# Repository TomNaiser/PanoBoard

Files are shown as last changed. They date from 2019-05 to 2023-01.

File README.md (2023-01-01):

# PanoBoard
Integrated Electronics Board for a Gigapixel Panorama Head (pan and tilt motion)
-Arduino nano based controller
-bluetooth communication with the windowsbased control notebook
-PID position control (modified RC-Servos)
-rotatory position encoders for precise position control 

The latest version PanoBoardV5 is a size-reduced version. With the shrunken electronics box the panorama rig fits into my photo backpack. 

Warning! The circuits in this project were designed as a hobbyist project and may contain unintentional mistakes.  I don't take any responsibility for damages caused by using the above circuit design. Please use the provided information at your own risk!

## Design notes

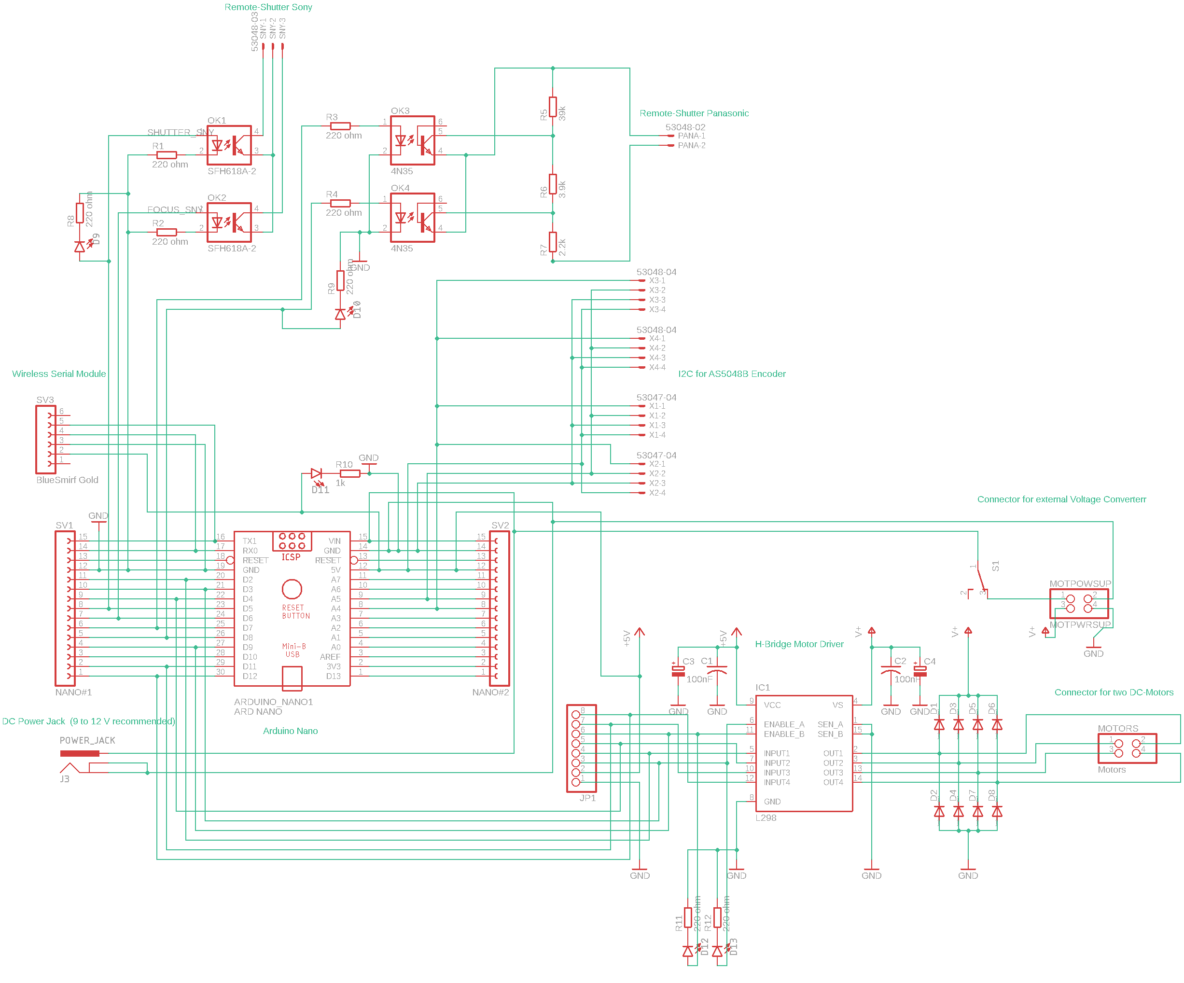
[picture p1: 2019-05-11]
PanoBoardSchematic.png

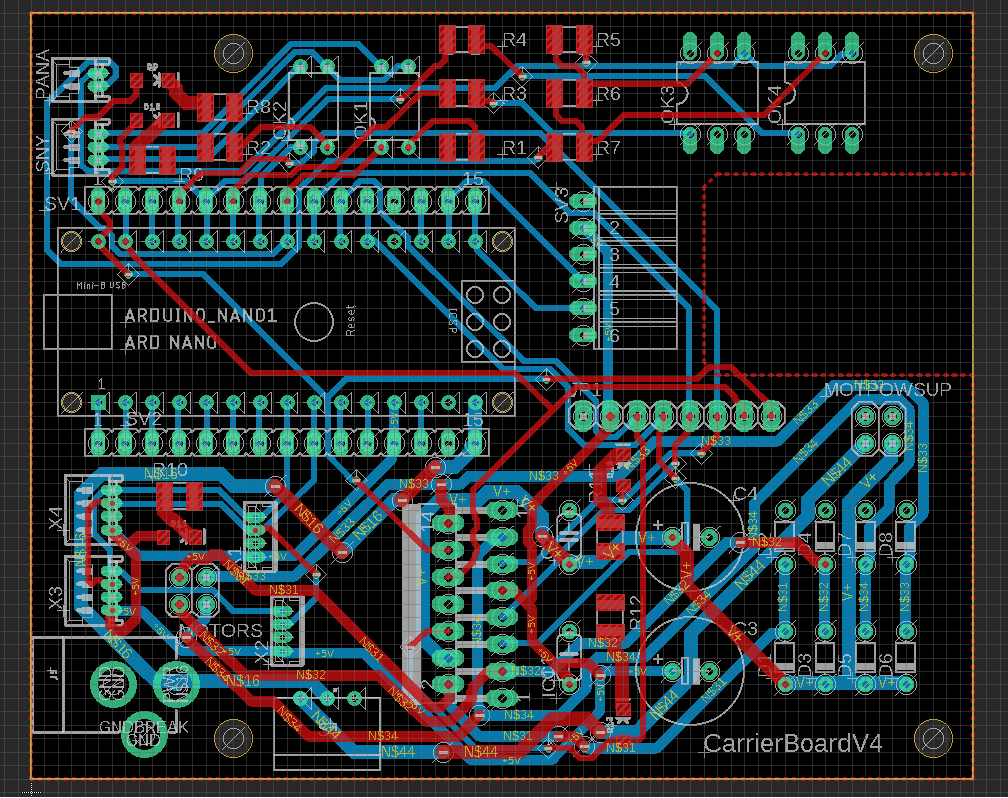
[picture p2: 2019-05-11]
PanoBoardV4_BoardLayout.PNG

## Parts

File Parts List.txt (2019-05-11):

From Amazon:
Arduino Nano Clone (1 piece)

Slide-Switch, MINI, ON-ON, RIGHT ANGLE 450302014072 By WURTH ELEKTRONIK  (1 piece)

SHOOT Rm-vpr1 remote shutter switch for Sony cameras (1 piece) (diassemble, you only need the connector to the camera, which looks like a usb, but actually isn't one)

Hitec Sail Winch Servo HS-785 HB (2 pieces)

From Servo City:
TM-700 Servo Gearbox with (I use a gear ratio of 3:1, however possibly 5:1 or 7:1 will enable better positioning accuracy) 
(2 pieces)

From Mouser:

1	
SparkFun Bluetooth Modem - BlueSMiRF Gold 474-WRL-12582  WRL-12582
1 piece

2	
Headers & Wire Housings Headers & Wire Housings 
437-8018300620001101
801-83-006-20-001101

3	
Magnetic Sensor Development Tools Magnetic Sensor Development Tools Adapter Board with I2C Interface
985-AS5048B-TS_EK_AB
AS5048B-TS_EK_AB
Adapter Board
2 pieces	

4	
DC Power Cords DC Power Cords PicoBlade CBL ASSY 14CKT 600MM NTL
538-15134-1406
15134-1406
PicoBlade CBL ASSY
1 or 2 pieces

5	
Headers & Wire Housings Headers & Wire Housings RIGHT ANGLE HDR 4P
538-53048-0410
53048-0410
RIGHT ANGLE HDR 4P

6	
Headers & Wire Housings Headers & Wire Housings VERTICAL HDR 4P
538-53047-0410
53047-0410
VERTICAL HDR 4P

7	
Headers & Wire Housings Headers & Wire Housings RIGHT ANGLE HDR 3P
538-53048-0310
53048-0310
RIGHT ANGLE HDR 3P

8	
Headers & Wire Housings Headers & Wire Housings RIGHT ANGLE HDR 2P
538-53048-0210
53048-0210
RIGHT ANGLE HDR 2P

9	
Headers & Wire Housings Headers & Wire Housings RECEPTACLE 4 POS
538-51021-0400
51021-0400
RECEPTACLE 4 POS

10	
Headers & Wire Housings Headers & Wire Housings RECEPTACLE 3 POS
538-51021-0300
51021-0300
RECEPTACLE 3 POS

11	
Headers & Wire Housings Headers & Wire Housings RECEPTACLE 2P
538-51021-0200
51021-0200
RECEPTACLE 2P

12	
SparkFun Accessories SparkFun Accessories DC Barrel Power Jack/Connector
474-PRT-00119
PRT-00119
1 piece

13	
Motor/Motion/Ignition Controllers & Drivers Motor/Motion/Ignition Controllers & Drivers Dual Full Bridge
511-L298
L298N
Dual Full Bridge
1 piece

14	
Transistor Output Optocouplers Transistor Output Optocouplers PTR 100%, 3.5KV
859-4N35
4N35
PTR 100%, 3.5KV
2 pieces

15	
Transistor Output Optocouplers Transistor Output Optocouplers Phototransistor Out Single CTR 63-125%
782-SFH618A-2
SFH618A-2
Phototransistor Out
2 pieces

16	
Schottky Diodes & Rectifiers Schottky Diodes & Rectifiers Vr/40V Io/1A AMMO
511-1N5819
1N5819
Vr/40V Io/1A AMMO
8 pieces

17	
Aluminium Electrolytic Capacitors - Radial Leaded Aluminium Electrolytic Capacitors - Radial Leaded 50volts 0.1uF 4x7 20% 1.5LS
647-USP1H0R1MDD
USP1H0R1MDD
50volts 0.1uF
2 pieces

18	
Aluminium Electrolytic Capacitors - Radial Leaded Aluminium Electrolytic Capacitors - Radial Leaded 100UF 100V
661-EKMQ101ELL101MJ1
EKMQ101ELL101MJ16S
100UF 100V
2 pieces

19	
Thick Film Resistors - SMD Thick Film Resistors - SMD 1210 220ohms 1% AEC-Q200667-ERJ-14NF2200U
ERJ-14NF2200U
1210 220ohms

20	
Thick Film Resistors - SMD Thick Film Resistors - SMD 1210 39Kohm 1% High Voltage
755-KTR25JZPF3902
KTR25JZPF3902
1210 39Kohm 1%

21	
Thick Film Resistors - SMD Thick Film Resistors - SMD 1210 3.9Kohms 1% AEC-Q200
667-ERJ-14NF3901U
ERJ-14NF3901U
1210 3.9Kohms

22	
Thick Film Resistors - SMD Thick Film Resistors - SMD 1210 2.2Kohms 5% AEC-Q200
667-ERJ-14YJ222U
ERJ-14YJ222U
1210 2.2Kohms

23	
Thick Film Resistors - SMD Thick Film Resistors - SMD CRGP 1210 1K0 1% SMD Resistor
279-CRGP1210F1K0
CRGP1210F1K0
CRGP 1210 1K0 1%

24	
Thick Film Resistors - SMD Thick Film Resistors - SMD CRGCQ 1210 2K7 1% SMD Resistor
279-CRGCQ1210F2K7
CRGCQ1210F2K7
CRGCQ 1210 2K7 1%

25	
Standard LEDs - SMD Standard LEDs - SMD 3.2X1.6MM LOW CRNT
604-APT3216LZGCK
APT3216LZGCK
3.2X1.6MM LOW CRNT

26	
Headers & Wire Housings Headers & Wire Housings 
437-8018705010001101
801-87-050-10-001101

27	
Headers & Wire Housings Headers & Wire Housings 25+25 DIL VERTICAL PIN HEADER GOLD HT
855-M20-9722545
M20-9722545
25+25 DIL VERTICAL

28	
Headers & Wire Housings Headers & Wire Housings 2.54MM 0.1" 15-PIN FEMALE HEADER
992-15FX1-254MM
15Fx1-254mm
2.54MM 0.1" 15-PIN

29	
Headers & Wire Housings Headers & Wire Housings KK 100 Hdr Assy RA B y RA Bkwy 06 Ckt Tin
538-22-28-7061
22-28-7061
KK 100 Hdr Assy RA B

30	
Headers & Wire Housings Headers & Wire Housings 50P SINGLE ROW
571-5-826629-0
5-826629-0
50P SINGLE ROW

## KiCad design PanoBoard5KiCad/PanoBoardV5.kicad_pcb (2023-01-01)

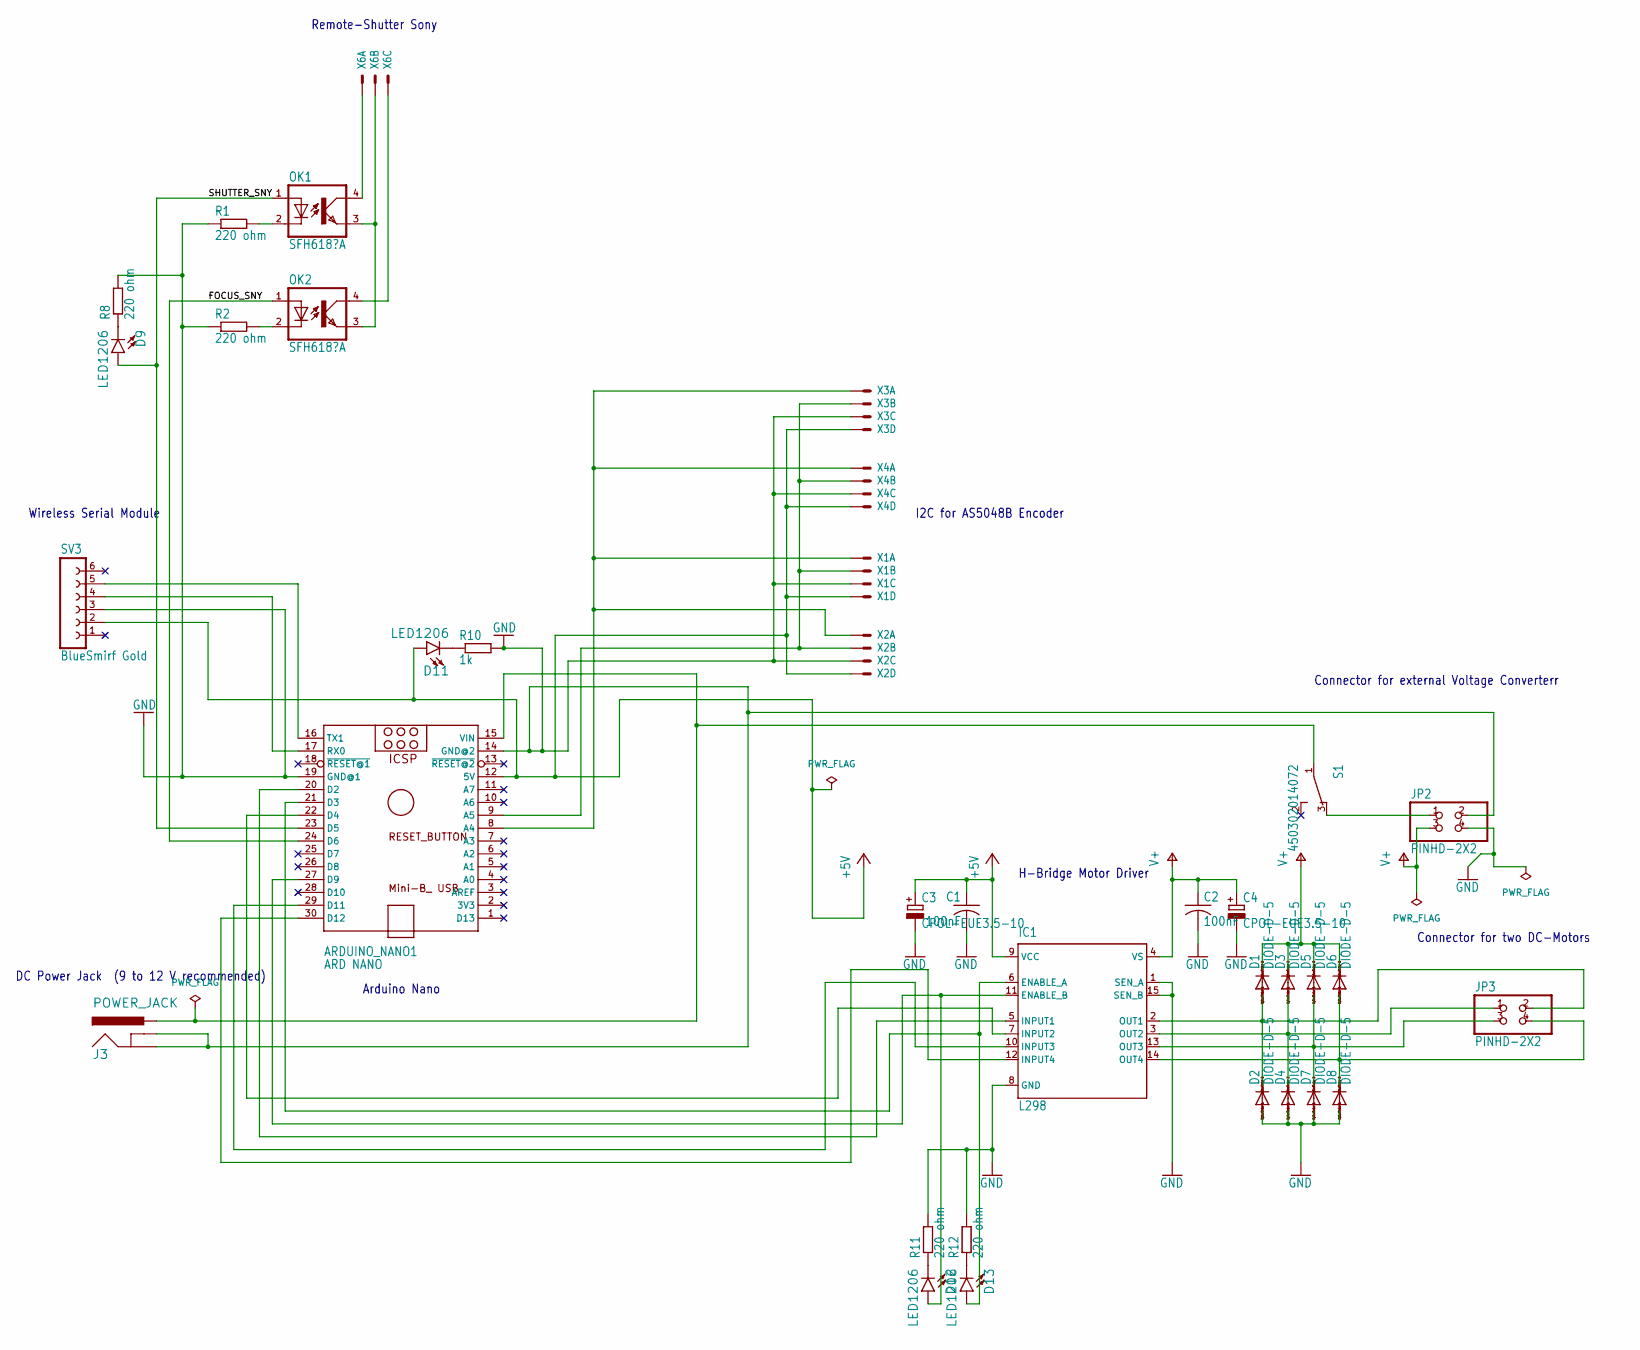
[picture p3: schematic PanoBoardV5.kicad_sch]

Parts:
ARDUINO_NANO1: ARD NANO; ARDUINO_NANO
C1, C2: 100nF; C050-024X044
C3, C4: CPOL-EUE3.5-10; E3,5-10
D1, D2, D3, D4, D5, D6, D7, D8: DIODE-D-5; D-5
D9, D11, D12, D13: LED1206; LED-1206
IC1: L298; MULTIWATT-15
J3: POWER_JACK; POWER_JACK_PTH
JP2, JP3: PINHD-2X2; 2X02
OK1, OK2: SFH618?A; DIP4
R1, R2, R8, R11, R12: 220 ohm; R1210
R10: 1k; R1210
S1: 450302014072
SV3: BlueSmirf Gold; FE06W
X1, X2: 53?-04047; 53047-04
X3, X4: 53?-04048; 53048-04
X6: 53?-03048; 53048-03

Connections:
+5V: ARDUINO_NANO1.12 (5V), C1.1, C3.+, D11.A, IC1.9 (VCC), SV3.2, X1.4 (S), X2.4 (S), X3.4 (S), X4.4 (S)
/FOCUS_SNY: ARDUINO_NANO1.24 (D6), OK2.1 (A)
/SHUTTER_SNY: ARDUINO_NANO1.23 (D5), D9.A, OK1.1 (A)
GND: ARDUINO_NANO1.14 (GND@2), ARDUINO_NANO1.19 (GND@1), C1.2, C2.2, C3.-, C4.-, D2.A, D4.A, D7.A, D8.A, IC1.1 (SEN_A), IC1.8 (GND), IC1.15 (SEN_B), J3.GND, J3.GNDBREAK, JP2.2, JP2.4, R1.1, R2.1, R8.2, R10.2, R11.2, R12.2, SV3.3, X1.3 (S), X2.3 (S), X3.3 (S), X4.3 (S)
unnamed: ARDUINO_NANO1.8 (A4), X1.1 (S), X2.1 (S), X3.1 (S), X4.1 (S)
unnamed: ARDUINO_NANO1.9 (A5), X1.2 (S), X2.2 (S), X3.2 (S), X4.2 (S)
unnamed: ARDUINO_NANO1.15 (VIN), J3.PWR, S1.1
unnamed: ARDUINO_NANO1.16 (TX1), SV3.5
unnamed: ARDUINO_NANO1.17 (RX0), SV3.4
unnamed: ARDUINO_NANO1.20 (D2), IC1.5 (INPUT1)
unnamed: ARDUINO_NANO1.21 (D3), D13.A, IC1.6 (ENABLE_A)
unnamed: ARDUINO_NANO1.22 (D4), IC1.7 (INPUT2)
unnamed: ARDUINO_NANO1.27 (D9), D12.A, IC1.11 (ENABLE_B)
unnamed: ARDUINO_NANO1.29 (D11), IC1.10 (INPUT3)
unnamed: ARDUINO_NANO1.30 (D12), IC1.12 (INPUT4)
unnamed: D1.A, D2.C, IC1.2 (OUT1), JP3.2
unnamed: D3.A, D4.C, IC1.3 (OUT2), JP3.1
unnamed: D5.A, D7.C, IC1.13 (OUT3), JP3.3
unnamed: D6.A, D8.C, IC1.14 (OUT4), JP3.4
unnamed: D9.C, R8.1
unnamed: D11.C, R10.1
unnamed: D12.C, R11.1
unnamed: D13.C, R12.1
unnamed: JP2.1, S1.3
unnamed: OK1.2 (C), R1.2
unnamed: OK1.3 (EMIT), OK2.3 (EMIT), X6.2 (S)
unnamed: OK1.4 (COL), X6.1 (S)
unnamed: OK2.2 (C), R2.2
unnamed: OK2.4 (COL), X6.3 (S)
V+: C2.1, C4.+, D1.C, D3.C, D5.C, D6.C, IC1.4 (VS), JP2.3

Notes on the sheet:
Connector for external Voltage Converterr
I2C for AS5048B Encoder
Connector for two DC-Motors
DC Power Jack (9 to 12 V recommended)
H-Bridge Motor Driver
Remote-Shutter Sony
Wireless Serial Module
Arduino Nano

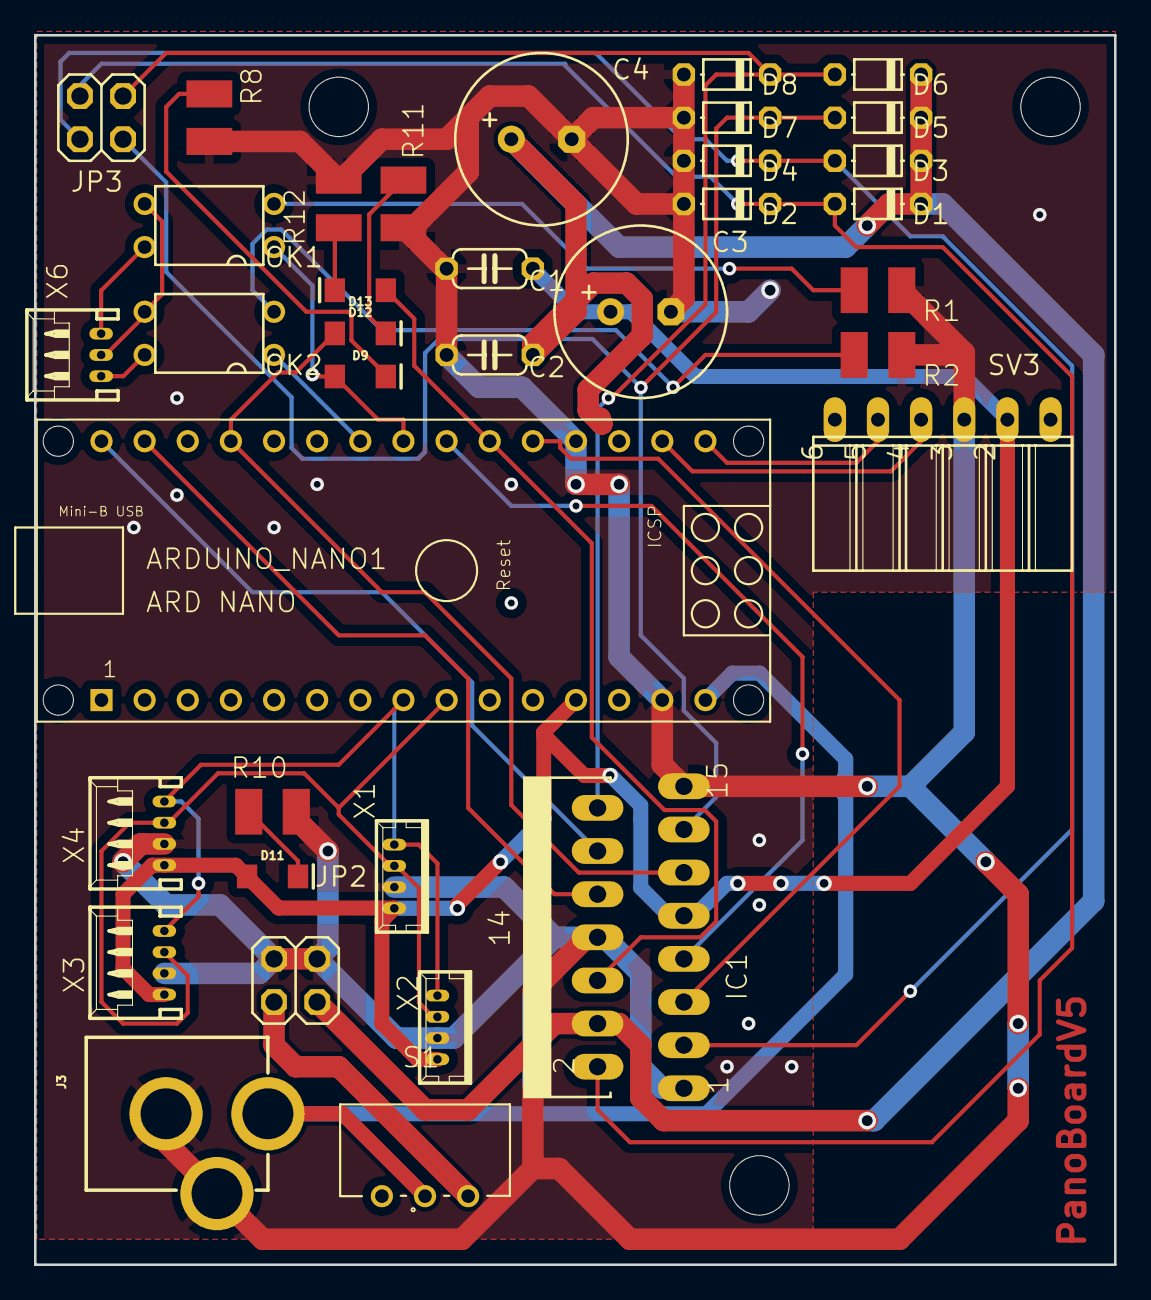
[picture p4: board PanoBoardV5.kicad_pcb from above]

Board: 2 copper layers, 63.6 x 72.4 mm, 39 parts (0 on the bottom side), 30 nets.

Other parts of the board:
@HOLE0, @HOLE2, @HOLE3: (no value)

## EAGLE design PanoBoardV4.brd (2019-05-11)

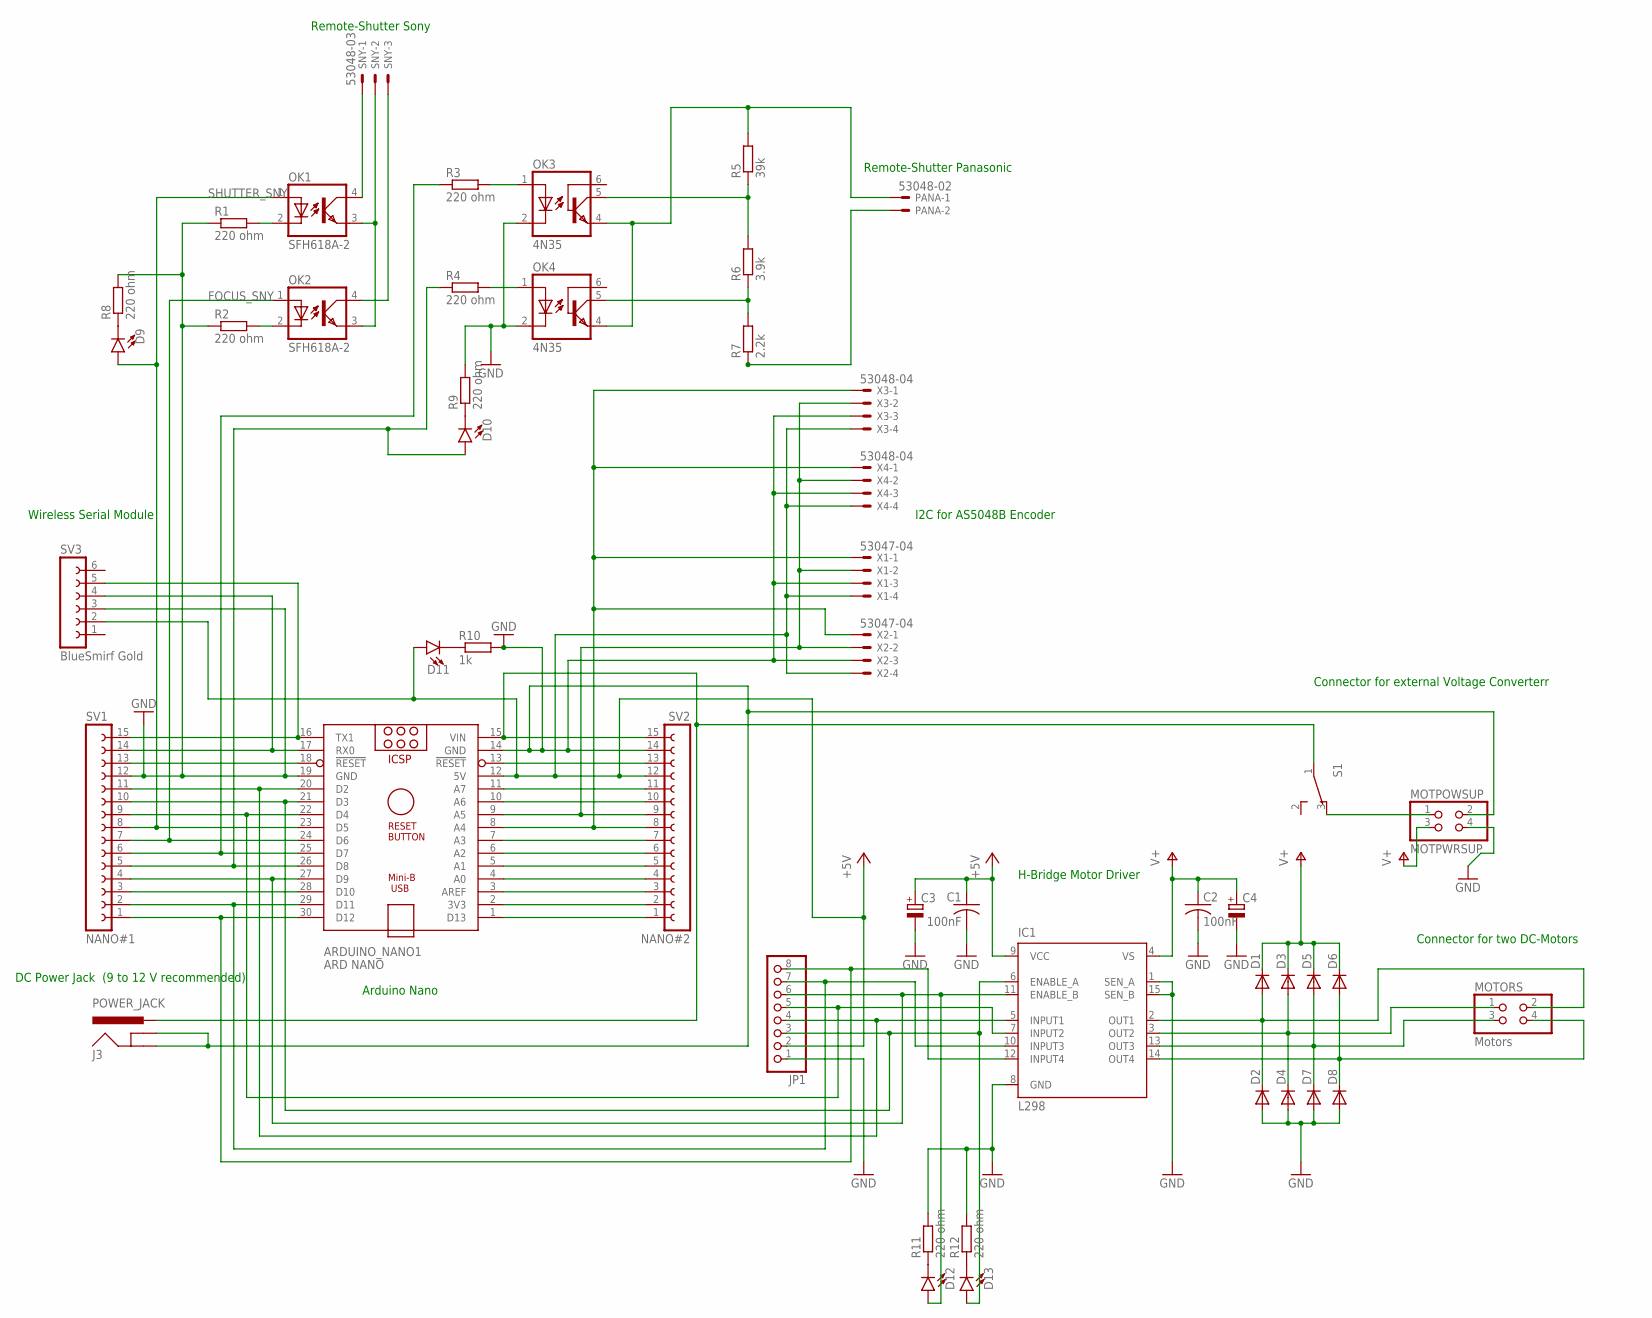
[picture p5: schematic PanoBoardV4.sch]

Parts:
ARDUINO_NANO1: ARD NANO; ARDUINO_NANO
C1, C2: 100nF; C050-024X044
C3, C4: CPOL-EUE3.5-10; E3,5-10
D1, D2, D3, D4, D5, D6, D7, D8: DIODE-D-5; D-5
D9, D10, D11, D12, D13: LED1206; LED-1206
IC1: L298; MULTIWATT-15
J3: POWER_JACK; POWER_JACK_PTH
JP1: PINHD-1X8; 1X08
MOTORS: Motors; 2X02
MOTPOWSUP: MOTPWRSUP; 2X02
OK1, OK2: SFH618A-2; DIP4
OK3, OK4: 4N35; DIL06
PANA: 53048-02
R1, R2, R3, R4, R8, R9, R11, R12: 220 ohm; R1210
R5: 39k; R1210
R6: 3.9k; R1210
R7: 2.2k; R1210
R10: 1k; R1210
S1: 450302014072
SNY: 53048-03
SV1: NANO#1; FE15
SV2: NANO#2; FE15
SV3: BlueSmirf Gold; FE06W
X1, X2: 53047-04
X3, X4: 53048-04

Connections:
+5V: ARDUINO_NANO1.12 (5V), C1.1, C3.+, D11.A, IC1.9 (VCC), JP1.2, SV2.12, SV3.2, X1.4, X2.4, X3.4, X4.4
FOCUS_SNY: ARDUINO_NANO1.24 (D6), OK2.1 (A), SV1.7
GND: ARDUINO_NANO1.14 (GND), ARDUINO_NANO1.19 (GND), C1.2, C2.2, C3.-, C4.-, D2.A, D4.A, D7.A, D8.A, IC1.1 (SEN_A), IC1.8 (GND), IC1.15 (SEN_B), J3.GND, J3.GNDBREAK, JP1.1, MOTPOWSUP.2, MOTPOWSUP.4, OK3.2 (C), OK4.2 (C), R1.1, R2.1, R8.2, R9.2, R10.2, R11.2, R12.2, SV1.12, SV2.14, SV3.3, X1.3, X2.3, X3.3, X4.3
unnamed: ARDUINO_NANO1.16 (TX1), SV1.15, SV3.5
unnamed: ARDUINO_NANO1.17 (RX0), SV1.14, SV3.4
unnamed: ARDUINO_NANO1.18 (!RESET), SV1.13
unnamed: OK1.2 (C), R1.2
unnamed: ARDUINO_NANO1.20 (D2), IC1.5 (INPUT1), JP1.4, SV1.11
unnamed: ARDUINO_NANO1.21 (D3), D13.A, IC1.6 (ENABLE_A), JP1.3, SV1.10
unnamed: ARDUINO_NANO1.22 (D4), IC1.7 (INPUT2), JP1.5, SV1.9
unnamed: OK1.3 (EMIT), OK2.3 (EMIT), SNY.2
unnamed: OK1.4 (COL), SNY.1
unnamed: ARDUINO_NANO1.25 (D7), R3.1, SV1.6
unnamed: ARDUINO_NANO1.26 (D8), D10.A, R4.1, SV1.5
unnamed: ARDUINO_NANO1.27 (D9), D12.A, IC1.11 (ENABLE_B), JP1.6, SV1.4
unnamed: ARDUINO_NANO1.28 (D10), SV1.3
unnamed: ARDUINO_NANO1.29 (D11), IC1.10 (INPUT3), JP1.7, SV1.2
unnamed: ARDUINO_NANO1.30 (D12), IC1.12 (INPUT4), JP1.8, SV1.1
unnamed: ARDUINO_NANO1.15 (VIN), J3.PWR, S1.1, SV2.15
unnamed: OK2.2 (C), R2.2
unnamed: ARDUINO_NANO1.13 (!RESET), SV2.13
unnamed: OK3.1 (A), R3.2
unnamed: ARDUINO_NANO1.11 (A7), SV2.11
unnamed: ARDUINO_NANO1.10 (A6), SV2.10
unnamed: ARDUINO_NANO1.9 (A5), SV2.9, X1.2, X2.2, X3.2, X4.2
unnamed: ARDUINO_NANO1.8 (A4), SV2.8, X1.1, X2.1, X3.1, X4.1
unnamed: ARDUINO_NANO1.7 (A3), SV2.7
unnamed: ARDUINO_NANO1.6 (A2), SV2.6
unnamed: ARDUINO_NANO1.5 (A1), SV2.5
unnamed: ARDUINO_NANO1.4 (A0), SV2.4
unnamed: ARDUINO_NANO1.3 (AREF), SV2.3
unnamed: ARDUINO_NANO1.2 (3V3), SV2.2
unnamed: ARDUINO_NANO1.1 (D13), SV2.1
unnamed: D1.A, D2.C, IC1.2 (OUT1), MOTORS.2
unnamed: D3.A, D4.C, IC1.3 (OUT2), MOTORS.1
unnamed: D6.A, D8.C, IC1.14 (OUT4), MOTORS.4
unnamed: D5.A, D7.C, IC1.13 (OUT3), MOTORS.3
unnamed: OK4.1 (A), R4.2
unnamed: OK2.4 (COL), SNY.3
unnamed: OK3.5 (COL), R5.1, R6.2
unnamed: OK3.4 (EMI), OK4.4 (EMI), PANA.1, R5.2
unnamed: OK4.5 (COL), R6.1, R7.2
unnamed: D9.C, R8.1
unnamed: PANA.2, R7.1
unnamed: D10.C, R9.1
unnamed: D11.C, R10.1
unnamed: MOTPOWSUP.1, S1.3
unnamed: D12.C, R11.1
unnamed: D13.C, R12.1
SHUTTER_SNY: ARDUINO_NANO1.23 (D5), D9.A, OK1.1 (A), SV1.8
V+: C2.1, C4.+, D1.C, D3.C, D5.C, D6.C, IC1.4 (VS), MOTPOWSUP.3

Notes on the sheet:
Remote-Shutter Panasonic
Remote-Shutter Sony
I2C for AS5048B Encoder
H-Bridge Motor Driver
Connector for external Voltage Converterr
Connector for two DC-Motors
Wireless Serial Module
Arduino Nano
DC Power Jack (9 to 12 V recommended)

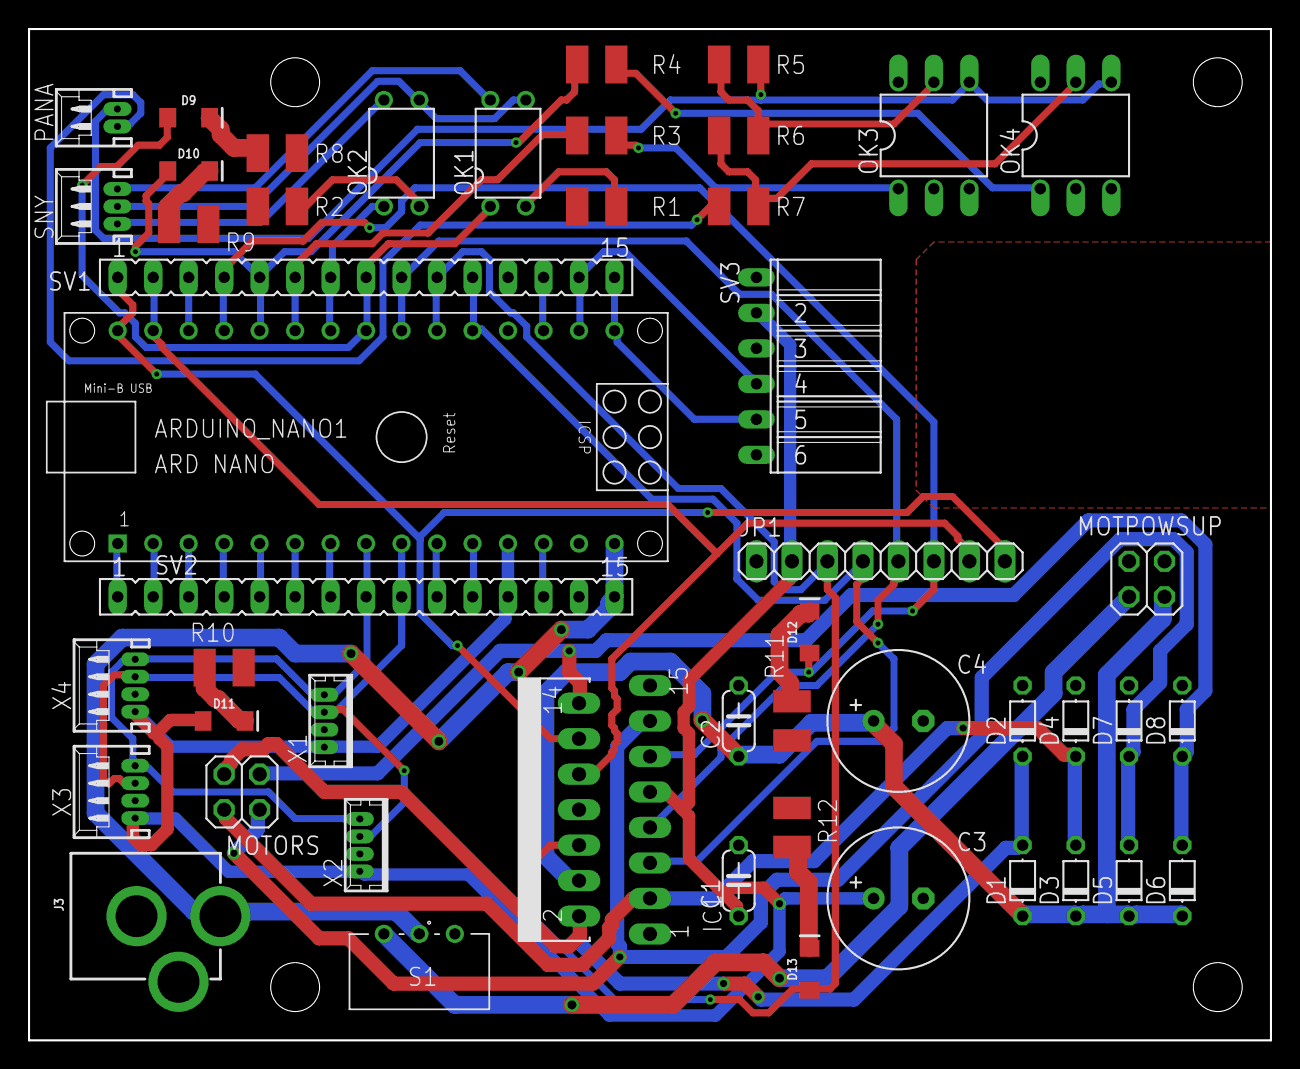
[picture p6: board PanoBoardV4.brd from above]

Board: 2 copper layers, 88.9 x 72.4 mm, 49 parts (0 on the bottom side), 51 nets.

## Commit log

2023-01-01 PanoBoardV5
    Simplified version of the board. Reduced footprint. Camera Triggering support only the Sony A7
    [PanoBoardV5.dsn, PanoBoardV5.kicad_pcb, PanoBoardV5.kicad_sch]
2023-01-01 Photos of the board

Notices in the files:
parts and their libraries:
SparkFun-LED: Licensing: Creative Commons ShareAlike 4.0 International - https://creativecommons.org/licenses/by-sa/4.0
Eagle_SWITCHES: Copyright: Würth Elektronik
